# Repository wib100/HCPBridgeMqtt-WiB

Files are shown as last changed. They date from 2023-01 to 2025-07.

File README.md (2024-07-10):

# Hörmann HCPBridge with MQTT and HomeAssistant Support


Emulates Hörmann UAP1-HCP board (HCP2= Hörmann communication protocol 2) using an ESP32 and a RS485 converter, and exposes garage door controls over web page and MQTT.

**Compatible with the following motors (UAP1-HCP / HCP2-Bus / Modbus):**

* SupraMatic E/P **Serie 4**
* ProMatic **Serie 4**
* [Rollmatic v2](docs/rollmatic_v2.md)

It is **not** compatible with E**3** series motors. Previous generations have different protocol (HCP1), different pin layout, and already have another supporting project (see [hgdo](https://github.com/steff393/hgdo), [hoermann_door](https://github.com/stephan192/hoermann_door) or [hormann-hcp](https://github.com/raintonr/hormann-hcp)).

## Functions

* Get current status (door open/close/position, light on/off)
* Support for ESP32-S1/S2/S3
* Support multiple HCP Bridges for multiple garage doors
* HomeAssistant integration via MQTT-AutoDiscovery
* Trigger actions via Webinterface
  * light on/off
  * gate open, close, stop
  * gate position: half, ventilation, custom (MQTT set_position compatible)
* Configuration (Wifi, MQTT, ...) via Web Interface
* Web Service [API](#web-service)
* OTA Update (with username and password)
* First Use Hotspot for configuration
* External (optional) sensor support (threshold orientated MQTT messages):
  * DS18X20 temperature sensor
  * BME280 temperature and humidity sensor
  * DHT22 temperature and humidity sensor
  * HC-SR04 proximity sensor (car (below) detection)
  * HC-SR501 PIR motion sensor
* Efficient MQTT traffic (send only MQTT Message if states changed)

## Web Interface

***http://[deviceip]***

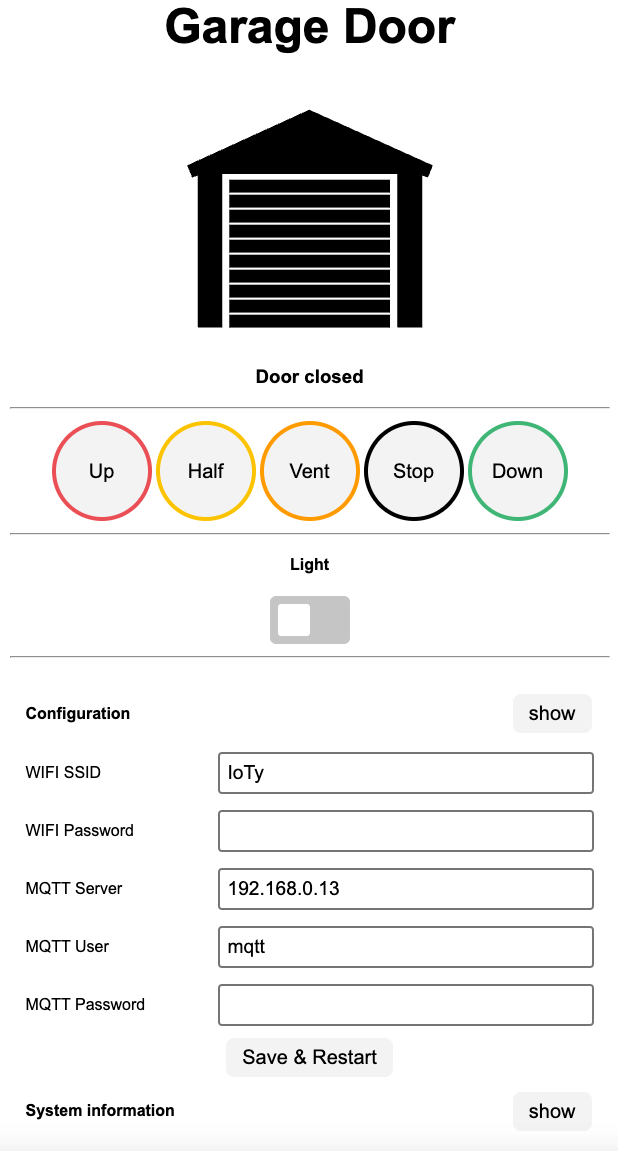
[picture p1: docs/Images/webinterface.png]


# Buy a ready to use kit [here](https://github.com/Gifford47/HCPBridgeMqtt/discussions/83) :rocket:

## ... or ...

# Build it yourself! 🔨

<details>
 <summary>Step 1: Wiring</summary>

  ## Wiring
 
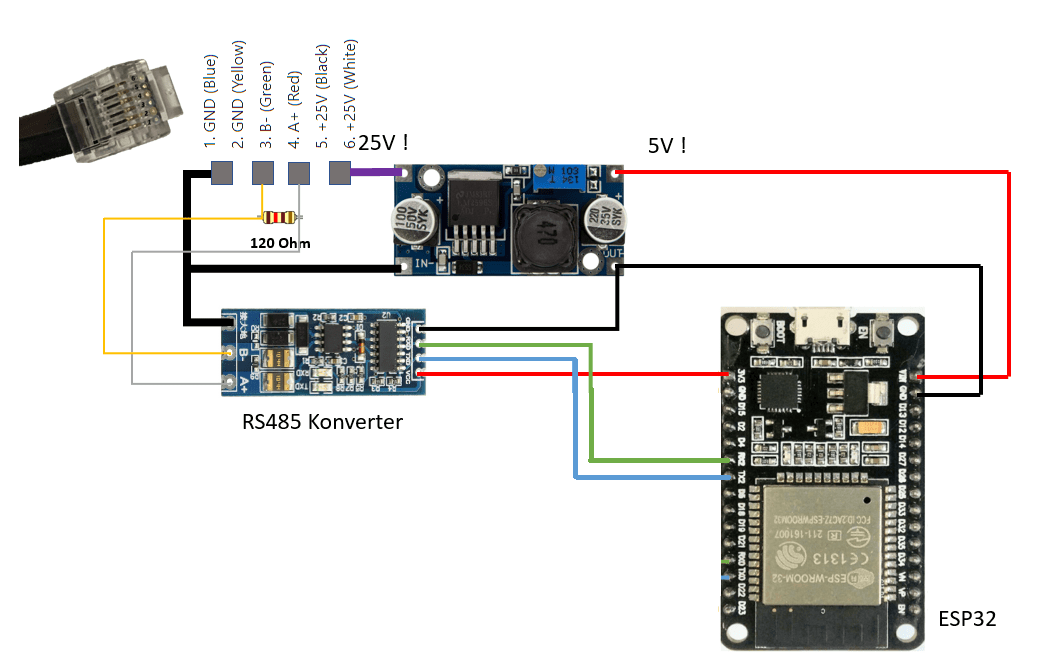
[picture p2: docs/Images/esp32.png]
min wiring
 
 
 ESP32 powering requires a Step Down Module such as LM2596S DC-DC, but any 24VDC ==> 5VDC will do, even the tiny ones with 3 pin.
 Please note that the suggested serial pins for serial interfacing, on ESP32, are 16 RXD and 17 TXD.

 <details>
 <summary>It is possible to implement it with protoboard and underside soldering:</summary>
 
 <br>
 
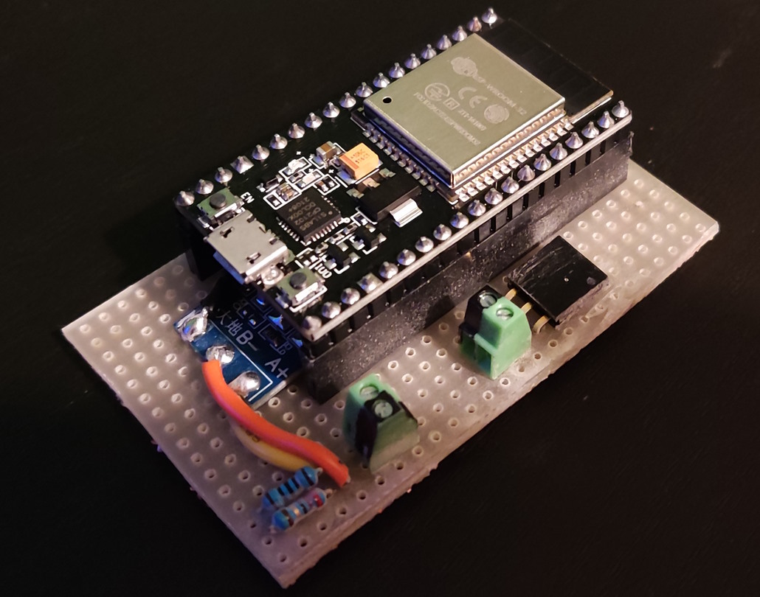
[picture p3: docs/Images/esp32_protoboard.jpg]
 
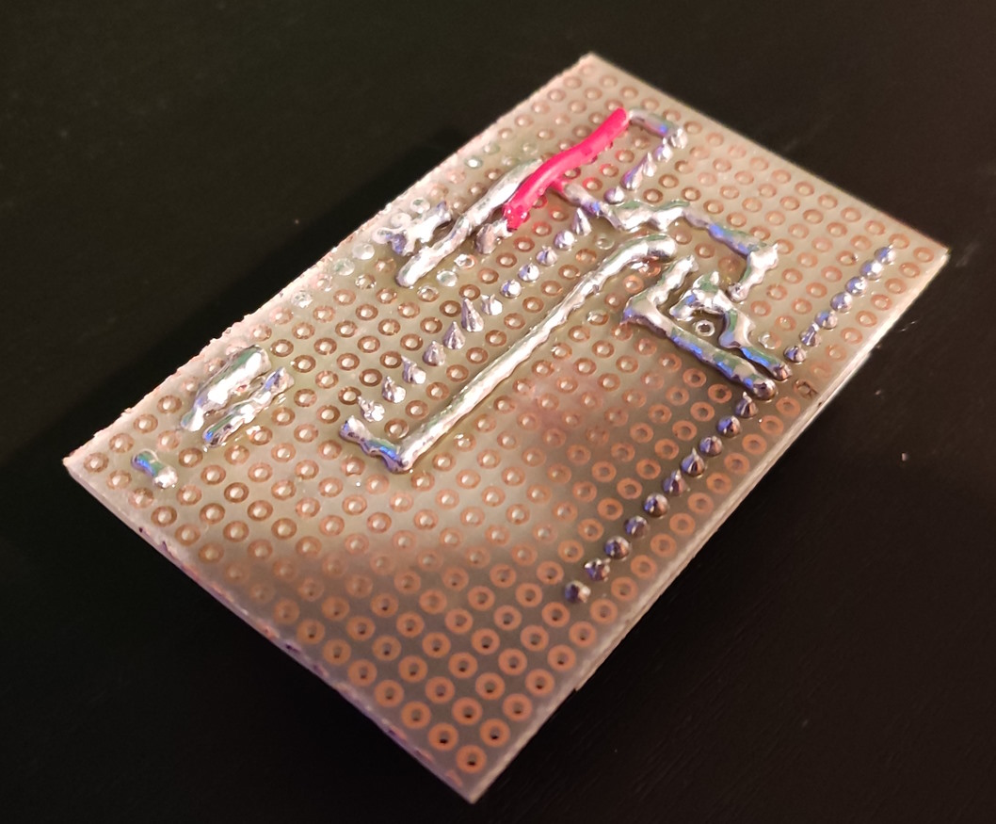
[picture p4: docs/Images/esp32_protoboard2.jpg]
 
 </details>
 
 <details>
 <summary>Details specific to Az-delivery ESP32 (ESP32-WROOM-32)</summary>
 Note the pinout on this cheap but widespread ESP32 module is a bit different. The GND on the bottom left must not be used (it is actually wrongly labeled, it should be CMD). Use the top right instead. Moreover use the pin 16 as RXD and pin 17 as TXD to match the code on this repository (using UART2, not UART0).
  
 
 
 </details>
 
 ## RS485
 
 <details open>
 <summary>Pinout RS485 Plug</summary>
 <br>
 
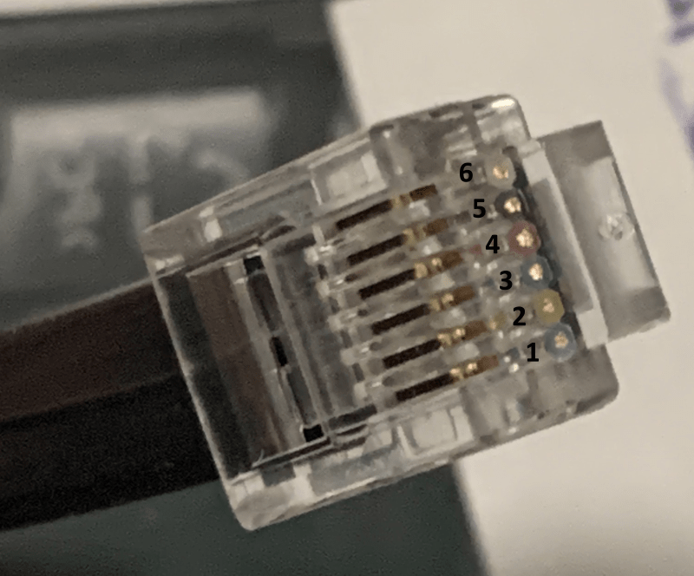
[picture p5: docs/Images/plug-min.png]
 
 
 > 📌 **Pinout**
 > 1. GND (Blue)<br>
 > 2. GND (Yellow)<br>
 > 3. B- (Green)<br>
 > 4. A+ (Red)<br>
 > 5. \+24V (Black)<br>
 > 6. \+24V (White)<br>
 
 </details>
 
 ### RS485 Adapter
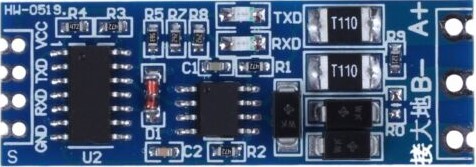
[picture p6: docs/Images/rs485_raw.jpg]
 
 > [!NOTE]<br>
 > Pins A+ (Red) and B- (Green) need a 120 Ohm resistor between them for BUS termination. Some RS485 adapters provide termination pad to be soldered.

</details><br>

<details>
 <summary>Step 2: Firmware upload</summary>
 
 ## Upload the firmware
 To use the board without any additional sensors (f.e. as showed in section [wiring](#wiring)) you only need to upload the standard firmware binary.
 ### Sensors
 
 To use additional sensors, you have also to build and upload the according firmware for the sensor. See [flash instructions](docs/flashing_instructions.md) for further info.
 <details>
 <summary>DS18X20 Temperature Sensor</summary>
 
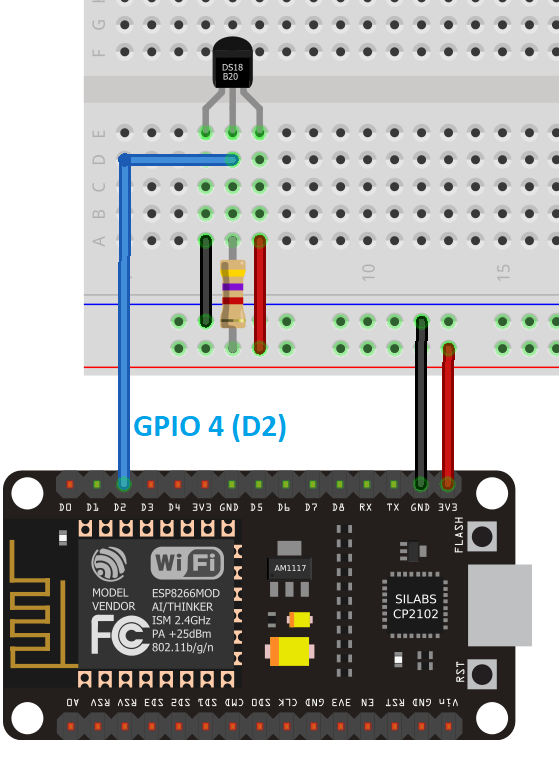
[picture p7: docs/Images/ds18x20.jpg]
  <br/>
 DS18X20 connected to GPIO4.
 <br>
 
 </details>
 
 <details>
 <summary>HC-SR501 PIR Motion sensor</summary>
 Digital out connected to GPIO23.
 <br>
 </details>
 
 <details>
 <summary>DHT22 Temperature and humudity Sensor</summary>
 Digital out connected to GPIO27.
 <br>
 </details>
 
 <details>
 <summary>BME280 Temperature and humudity Sensor</summary>
 
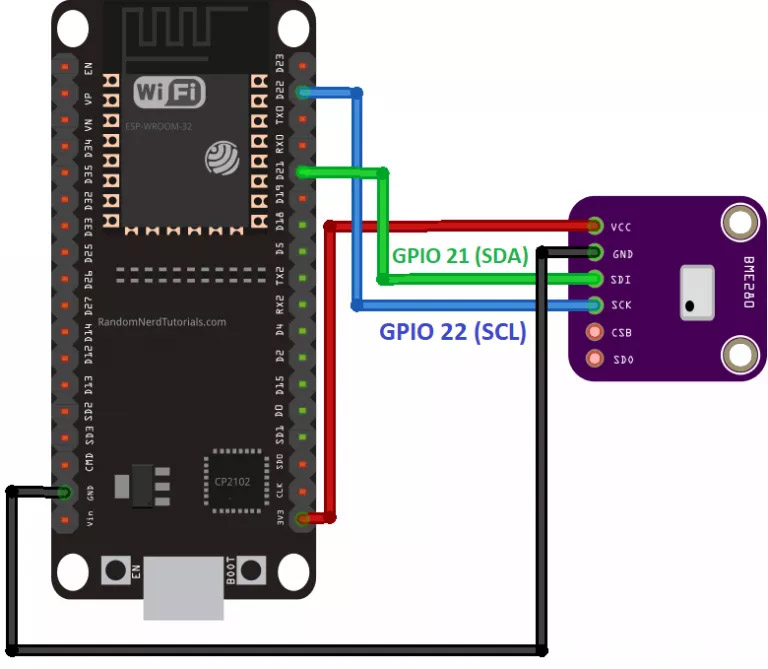
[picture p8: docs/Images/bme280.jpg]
  <br/>
 SDA connected to  GPIO21<br>
 SCL/SCK connected to GPIO22<br>
 <br>
 </details>
 
 <details>
 <summary>HC-SR04 Ultra sonic proximity sensor</summary>
 
 <br>
 Use the project task for HC-SR04.
 The wiring pins are:<br>
 SR04 Trigger pin is connected to GPIO5<br>
 SR04 ECHO pin is connected to GPIO18<br><br>
 
 It will send an mqtt discovery for two sensor one for the distance in cm available below the sensor and the other informing if the car park is available. It compare if the distance below is less than the maximal measured distance then car park is not available. The hcsr04_maxdistanceCm is defined with 150cm in configuration.h. This setting might not work for everyone. Change it to your needs.
 
 </details>
</details><br>

<details>
  <summary>Step 3: Configuration</summary>

  ## Configuration
  At first boot the settings from the configuration.h file are taken over as user preferences. If you choose to make your own build you can setup your settings there.
  After first boot you can change your settings directly in the Web interface without the need to create a new build. 
  
  With the default configuration it will open a Wifi Hotspot you can connect to. When connected to it you can use the url http://192.168.4.1 in a webbrowser to access the Web Interface and configure the device.
  
  Use the Basic Configuration section to set your wifi and MQTT credentials, after hitting the Save button your device will reboot.
  The Password fields are redacted if there are set with a *. If you don't want to change it just leave the * as it will be interpretet as no change.
  
  
  
  The preferences will stay even after a OTA update.
  When the memory of your ESP get's deleted your ESP will again load the settings from the configuration.h file.
  
  You can reset all preferences by pressing the BOOT button on the ESP for longer then 5 Seconds and releasing it.
  This will reset all preferences to the default values from configuration.h in the flashed firmware build.
  
  ## Web Services
  
  <details>
  <summary>Send commands</summary>
  
  URL: **http://[deviceip]/command?action=[id]**
  <br>
  
  | id | Function | Other Parameters
  |--------|--------------|--------------|
  | 0 | Close | |
  | 1 | Open | |
  | 2 | Stop | |
  | 3 | Ventilation | |
  | 4 | Half Open | |
  | 5 | Light toggle | |
  | 6 | Restart | |
  | 7 | Set Position | position=[0-100] |
  
  </details>
  
  <details>
  <summary>Status report</summary>
  
  URL: **http://[deviceip]/status**
  <br>
  
  Response:
  ```
  {
  "valid": true,
  "doorstate": 64,
  "doorposition": 0,
  "doortarget": 0,
  "lamp": false,
  "temp": 19.94000053,
  "lastresponse": 0,
  "looptime": 1037,
  "lastCommandTopic": "hormann/garage_door/command/door",
  "lastCommandPayload": "close"
  }
  ```
  </details>
  
  <details>
  <summary>Wifi status</summary>
  
  URL: **http://[deviceip]/sysinfo**
  <br>
  </details>
  
  <details>
  <summary>OTA Firmware update</summary>
  
  URL: **http://[deviceip]/update**
  <br>
  
  
  
  </details><br>
  
  </details><br>

<details>
  <summary>Step 4: Installation and Bus Scan</summary>
 
  ## Installation
  
  * Connect the board to the BUS
  * Run a BUS scan (differs on the following hardware version): 
  
  ### Old Hardware version
  
  BUS scan is started through flipping (ON - OFF) last dip switch. Note that BUS power  (+24v) is removed when no devices are detected. In case of issues, you may find useful to "jump start" the device using the +24V provision of other connectors of the motor control board.
    
  ### New Hardware version 
  With newer HW versions, the bus scan is carried out using the LC display in menu 37. For more see: [Supramatic 4 Busscan](https://www.tor7.de/news/bus-scan-beim-supramatic-serie-4-fehlercode-04-vermeiden)
  
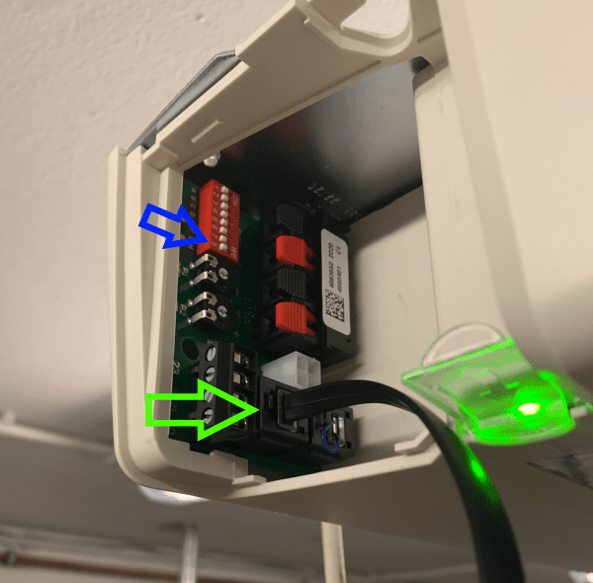
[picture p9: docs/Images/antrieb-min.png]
  
</details><br>

## Set the ventilation position 

This is just a quick and dirty implementation and needs refactoring, but it is working.
Using the Shutter Custom Card (from HACS) it is also possible to get a representation of the current position of the door, and slide it to custom position (through set_position MQTT command).

The switch for the venting position works with a small hack. Based on the analyses of dupas.me the motor should gave a status 0x0A in venting position. As this was not the case the variable VENT_POS in hciemulator.h was default with value '0x08' which correspond to the position when the garage door is in venting position (position available under ***http://[deviceip]/status***). When the door is stopped in this position the doorstate is set as venting.

<details>
<summary>HomeAssistant shutter cards</summary>

<br>

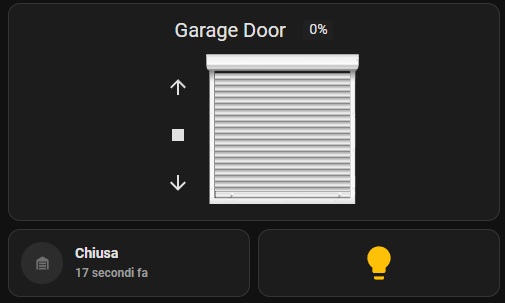
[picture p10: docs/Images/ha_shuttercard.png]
Homeassistant card1

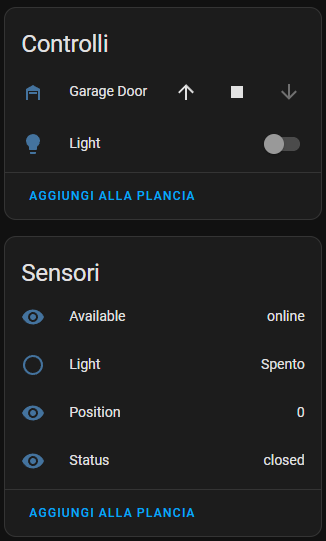
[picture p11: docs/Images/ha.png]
Homeassistant card2

</details>

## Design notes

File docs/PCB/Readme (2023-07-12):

Many thanks @vladimirzrnic for sharing his PCB design.

In the archive folder you will find a working design but to big to fit in the enclosure.

Please always check your wiring as depending on the cable or on the connector on the board the wires could be inverted. More detailed howto will follow

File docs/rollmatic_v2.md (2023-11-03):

# Rollmativ V2

## Hardware part:

* Remove power cord
* Plug in RJ-11 connector
* Plug-in power cord
* Drive the garage door completely up or down once

## Programming:

* Hold "PGR" button until 10 is shown
* Press "Down" button until "37" is shown
* Press "PRG" button once -> Display shows "00" (meaning "no external modules configured")
* Press "Up" button once until 01 is shown (meaning "configure external module")
* Hold "PGR" button until "B.S." is shown
* When "B.S." starts blinking, bus scan is running (RX and TX on RS485 board active)
* If external module was recognized on the bus, the display shows "1" for a couple of seconds
* If external module was not recognized on the bus, the display shows "01" or "00" for a couple of seconds
* Menu goes back to "10"

## Troubleshooting Error "04"
Hörmann Rollmatic v2 uses HCP2-Bus which requires external modules to be registered and unregistered via bus scan. Error "04" shows up when you want to drive the door, but the registered external module was removed without performing a bus scan afterwards. The door will not drive until the issue is solved.

This can be archieved by Powering off the door, re-attach the external module and power on again.
Or by performing a complete factory reset of the Rollmatic v2.

Unfortunately a simple un-registration of a registered (but non working or non-attached module) seems not possible since in my case, Error "04" prevents access to the programming menu after powering on.

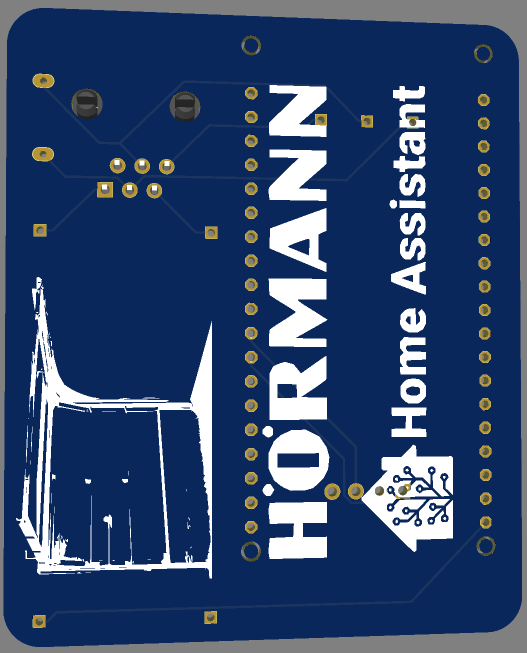
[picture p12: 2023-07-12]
docs/PCB/vladimirzrnic/back.png

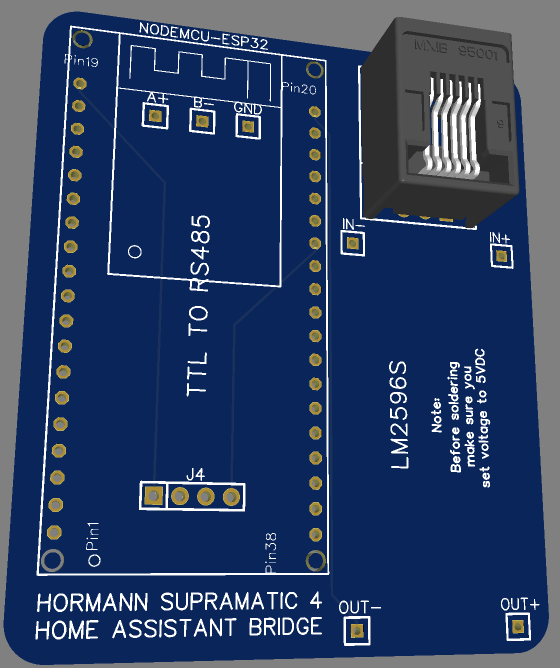
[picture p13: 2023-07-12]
docs/PCB/vladimirzrnic/top.png

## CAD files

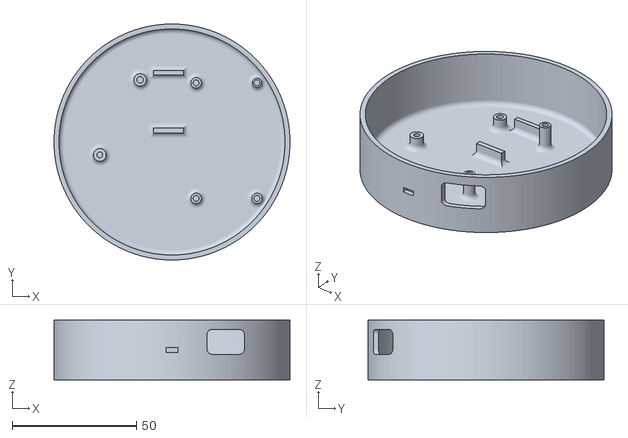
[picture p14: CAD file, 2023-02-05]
docs/3d/body.STL
95.0 x 95.0 x 24.0

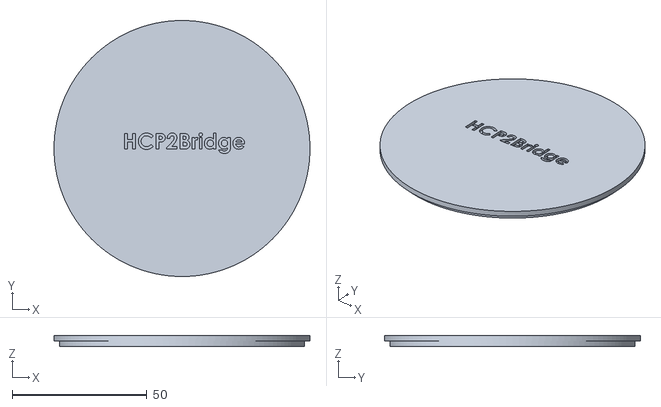
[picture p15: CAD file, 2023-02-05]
docs/3d/lid.STL
95.0 x 95.0 x 4.00

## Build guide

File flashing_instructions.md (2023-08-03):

# How to Flash the Firmware

## Setup Software

Download and install VS Code from Microsoft to your Computer: https://code.visualstudio.com/download

After that open VS Code and go to extensions, search for Platform IO and install it, follow any instructions if a restart or something is needed

## Get Firmware

On the Main Repo click the green Get Code Button and download the firmware as a zip.
Extract the Zip File and remember where you put it on your Computer.
Go to VSCode, click the PlatformIO Symbol at the bottom to switch to the Plugin UI.
Click the Open Folder button and select the HCPBridgeESp32 Folder inside the extracted Firmware.

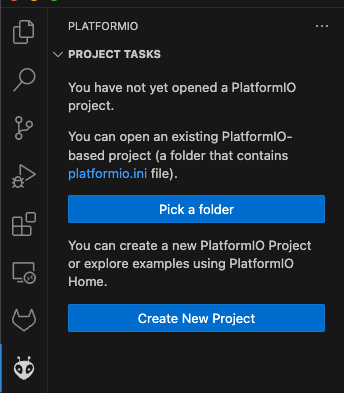
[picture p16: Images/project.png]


## Configuration

Use the left Sidebar again and click on the Folder Symbol to switch to the File List.
Before you can flash the Firmware you will need to change the Configuration in the configuration.h File located in the src Folder.

You need to set your WIFi Name/SSID and Password as well as the Connection Details to your MQTT Server if you want to use that Feature.

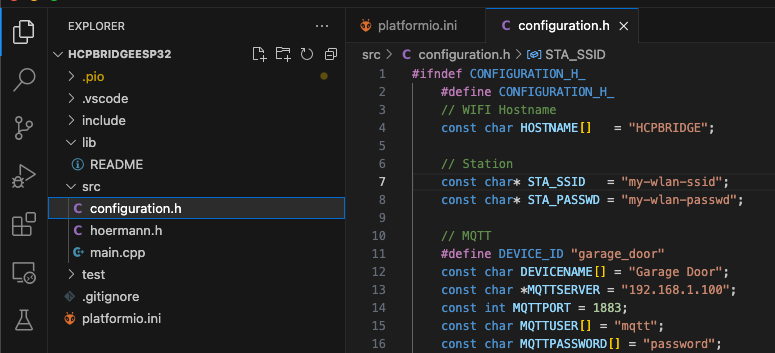
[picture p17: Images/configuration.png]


## Build and Flash

Go back to the Platform IO UI and click on the ESP Model you got under "Project Tasks".
ESP32 for older Boards and ESP32S3 for newer Boards (for example all PCBs with a Tynet logo)
Open the General Tasks of the Board you got and click Build.

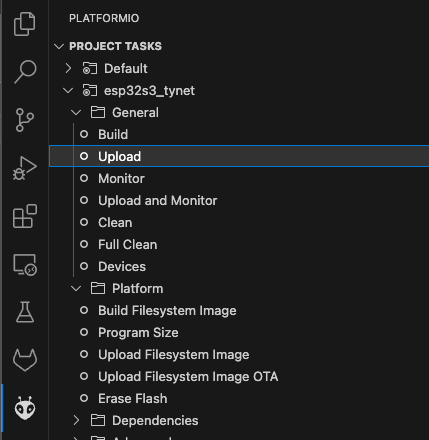
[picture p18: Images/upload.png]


This should prepare the Firmware for your Board including your Configuration, if all goes well the Terminal will show a green success message.

If this works you can connect your Device and click the Upload Task to flash it, this should also result in a Success info in green text inside the Terminal.

After this you can replug your device from USB to restart it and it should connect to your WIFI Router and MQTT Server.

Now you can connect it via the RJ12 cable to your garage door and start the BUS Scan, if all works the two communication leds should blink fast.
With this the MQTT as well as web controls on the devices IP should also work and you are Done :)

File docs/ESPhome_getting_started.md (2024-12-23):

# Getting started with the ESPHome version

Our boards from tynet.eu ship with the normal Arduino based Firmware that is simple to use out of the box.
Sadly this software that was developed over the past years got some minor inconveniences that are not simple to fix.
If you are one of the few people that have an issue with th software or just wan't to use ESPHome instead you can follow this guide

ESPHome uses a native Home Assistant API instead of MQTT and is simple to setup, we also porivde configuration files as well as ready to flash bin files for our boards.

## Setup ESPHome in Home Assistant

You can follow the [official guide](https://esphome.io/guides/getting_started_hassio) to install the ESPHome Add-on for Home Assistant.

The main steps are:

1. Open your Home Assitant UI
2. Go to Settings->Add-Ons->Add-on Store and search for ESPHome
3. Install and activate the ESPHome addon

## Upgrade from non ESPHome firmware

Our boards all ship with a non ESPHome based firmware, it can be upgraded really simple.

1. Ensure your board is powered over USB-C 
2. Download ESPHome based firmware file: [hcpbridge.ota.bin](https://github.com/Tysonpower/HCPBridgeMqtt_tynet/raw/refs/heads/main/hcpbridge.ota.bin)
3. Connect to your board and open the OTA webui: [http://192.168.4.1/update](http://192.168.4.1/update)
4. If asked use the following credentials to login: `user: admin pass: admin`
5. Click "Select File", navigate to the downloaded ota file from step 1, 

## Board Setup

### Using USB (recommended)

1. Ensure your board is connected to your PC over USB-C
2. Open [web.ESPHome.io](https://web.esphome.io), click connect, select the ESP32-S3 device from the list
3. Click the 3 point menu and select Configure Wifi, select or anter your wifi name and password


4. After entering your wifi credentials click connect


### Using WiFi

1. Ensure your board is powered over USB-C
2. Search and connect to the wifi called `hcpbridge`
3. Open http://192.168.4.1 when connected, login is `user: admin pass: tynet.eu`
4. Connect to your wifi network over the UI
____

Now your board should be connected to your home network over wifi.

Open home Assistant, go to Devices, here the garage door should be visible under discovered devices, just click "Add".



## Change preflashed config (Optional)

1. open home assistant and go to the ESPHome UI under Add-Ons
2. You should see the dicovered device, press take control. if you like, change the name


4. it will ask to update the device with encryption, click install, it will take a wile to build the new firmware


5. When it finished uploading you will see the following log output, if this is the case you can press close and you are done


In some cases you need to set your wifi credentials again afterwards like before

## Setup ESPHome in Home Assistant from scratch

1. Open ESPHome in Home Assistant
2. Connect your board only via usb to your PC
3. Click "New Device" and enter a name


4. Click ESP32-S3


5. Copy and save the displayed encryption key and click skip


6. Click on the secrets button on the top right, create the following keys and enter your wifi credentials as well as the secret api key you just copied, hit save

```
wifi_ssid: "myWifi"
wifi_password: "myWifiPassword"
api_key: "myApiSecretWeCopiedAfewMinutesAgo"
web_username: "admin"
web_password: "tynet.eu"
hcp_wifi_ap_password: "tynet.eu"
```

7. Click Edit on the device card


8. Copy paste the content of the ESPHome.yaml file from this repo into the editor, click save


9. Click install, then select Manual download, wait for the firmware to be build, select factory format to get the.bin file




10. Then go to [web.ESPHome.io](https://web.esphome.io/), click connect and select your ESP from the device list, click INSTALL, select the .bin file you just downloaded and click Install.
If it doesen't work, try it multiple times


11. go back to home assistant, open settings->devices->ESPHome, here you should be able to add the device, if not try to powercycle the board


Click done and you can now use the Device


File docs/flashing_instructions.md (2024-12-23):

# How to Flash the Firmware

## Setup Software

Download and install VS Code from Microsoft to your Computer: https://code.visualstudio.com/download

After that open VS Code and go to extensions, search for Platform IO and install it, follow any instructions if a restart or something is needed

## Get Firmware

On the Main Repo click the green Get Code Button and download the firmware as a zip.
Extract the Zip File and remember where you put it on your Computer.
Go to VSCode, click the PlatformIO Symbol at the bottom to switch to the Plugin UI.
Click the Open Folder button and select the HCPBridgeESp32 Folder inside the extracted Firmware.



## Configuration

In this step you can preset the preferences. On first boot they will be stored on the Memory of the ESP. 
After you have to change it from the WEB ui or Reset the ESP memory to load again the data from the configuration file.
Use the left Sidebar again and click on the Folder Symbol to switch to the File List.
Before you can flash the Firmware you will need to change the Configuration in the configuration.h File located in the src Folder.

You need to set your WIFi Name/SSID and Password as well as the Connection Details to your MQTT Server if you want to use that Feature.



## Build and Flash

Go back to the Platform IO UI and click on the ESP Model you got under "Project Tasks".
ESP32 for older Boards and ESP32S3 for newer Boards (for example all PCBs with a Tynet logo)
Open the General Tasks of the Board you got and click Build.



This should prepare the Firmware for your Board including your Configuration, if all goes well the Terminal will show a green success message.

If this works you can connect your Device and click the Upload Task to flash it, this should also result in a Success info in green text inside the Terminal.

After this you can replug your device from USB to restart it and it should connect to your WIFI Router and MQTT Server.

Now you can connect it via the RJ12 cable to your garage door and start the BUS Scan, if all works the two communication leds should blink fast.
With this the MQTT as well as web controls on the devices IP should also work and you are Done :)

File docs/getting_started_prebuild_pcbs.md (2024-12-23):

# Getting started with prebuild PCBs

If you bought a prebuild PCB from either Tynet.eu or someone else you can follow this setp by step guide to setup your HCP-Bridge with your Hörmann Garage Door.
These instructions focus on the tynet.eu PCB version, but it will be really similar with all PCBs.

You want to connect temperature sensors or something else? See our guide: [Connecting sensors on tynet boards](connecting_sensors_prebuild_pcbs.md)

## What you need

* Prebuild PCB with HCPBridge Firmware installed (installed out of the box on tynet.eu PCBs)
* USB-C power supply

## Initial configuration

### 1. Connect the PCB to power via the USB-C connector and wait a few seconds. the 3V3 LED will be lit.
### 2. Search and connect to the WIFI Network called "HCPBRIDGE" the PCB creates with a phone or pc.
### 3. When connected, open a webbrowser and go to the WEBUI under the following url : http://192.168.4.1

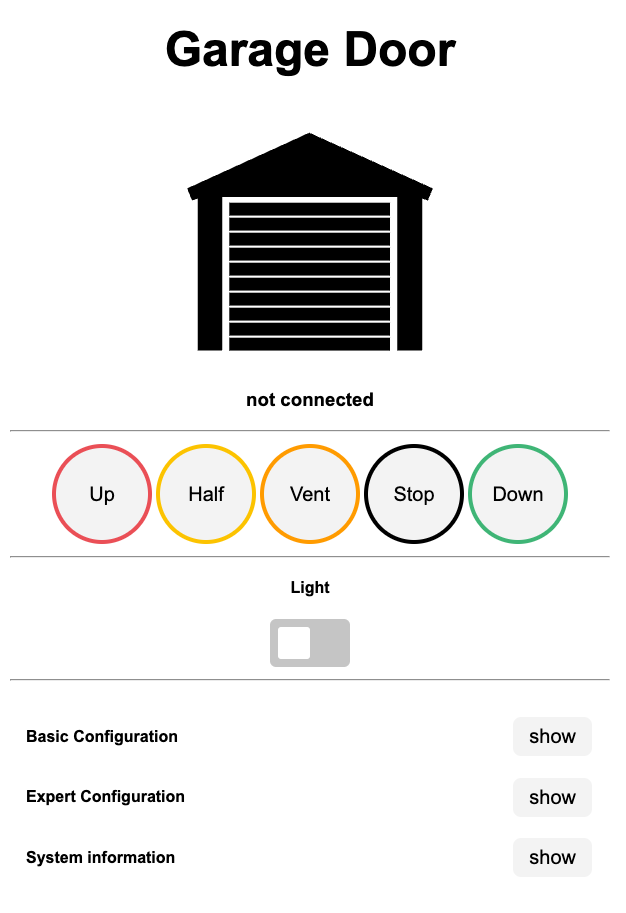
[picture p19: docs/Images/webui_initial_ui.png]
Initial WebUI


### 4. Open the "Basic Configuration" tab and enter your WIFI and MQTT credentials, then click save.

> Note: The wifi password has to be ASCII chars between ASCII 32-126.

> Tip: To disable the wifi AP just uncheck the "Enable wifi AP" checkbox and save

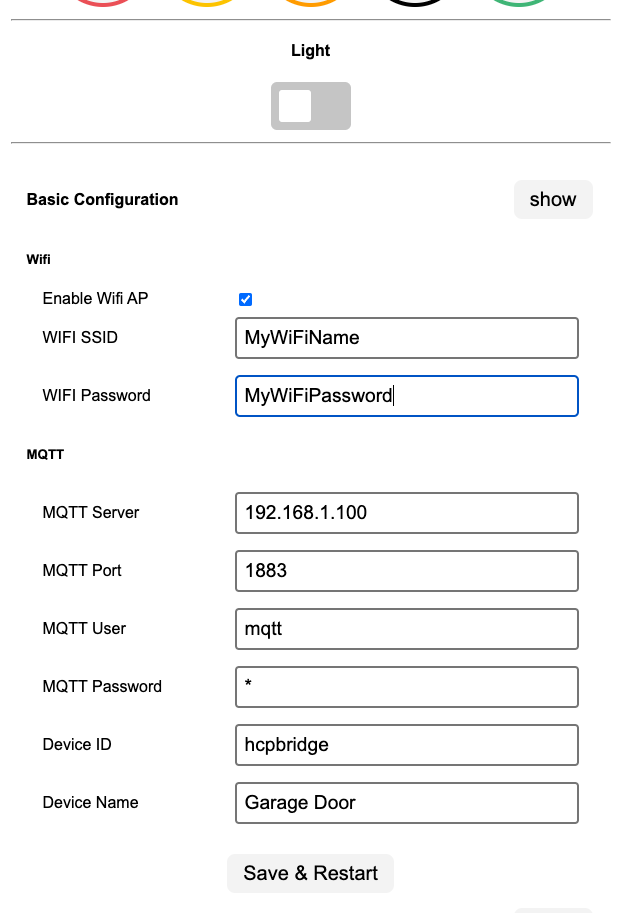
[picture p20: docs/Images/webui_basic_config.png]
basic config


### 5. The PCB should now be connected to your wifi. You can now check if it is reachable from your home network and if it connected to your MQTT Server.

## Installation

### 1. connect the PCB with a RJ12 cable to the BUS port on your Hörmann garage door motor (image below, see green arrow).

Garage Motor
   
### 2. Figure out how to execute a bus scan on your model, see info below or have a look in your motors ueer manual.

**ProMatic Serie 4**

Use the bottom dip switch (see image above, blue arrow) and toggle it, this will start the buss can.

**SupraMatic E/P Serie 4**

Use the Buttons to navigate to the menu 37 and excecute the Bus Scan, see here: [Tor7.de - Supramatic Bus Scan](https://www.tor7.de/news/bus-scan-beim-supramatic-serie-4-fehlercode-04-vermeiden)
  
### 3. execute a bus scan on your garage door motor, this should make the PCB light up (3V3) and blink rapidly (RS485 module)
### 4. if the bus scan was succesfully you can connect to the WEBUI and control your garage door motor, it should look like in the image below.

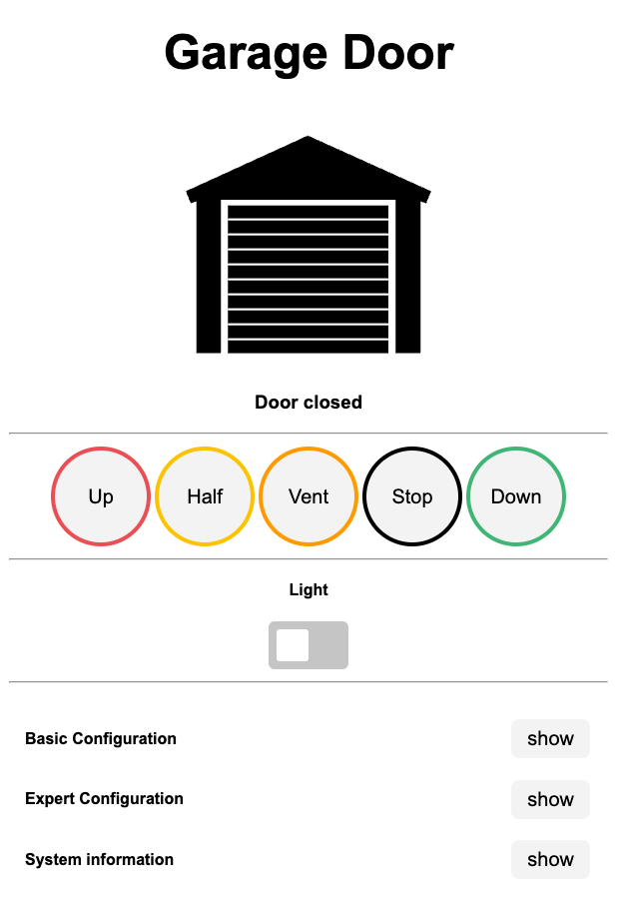
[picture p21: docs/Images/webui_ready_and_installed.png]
Installation done


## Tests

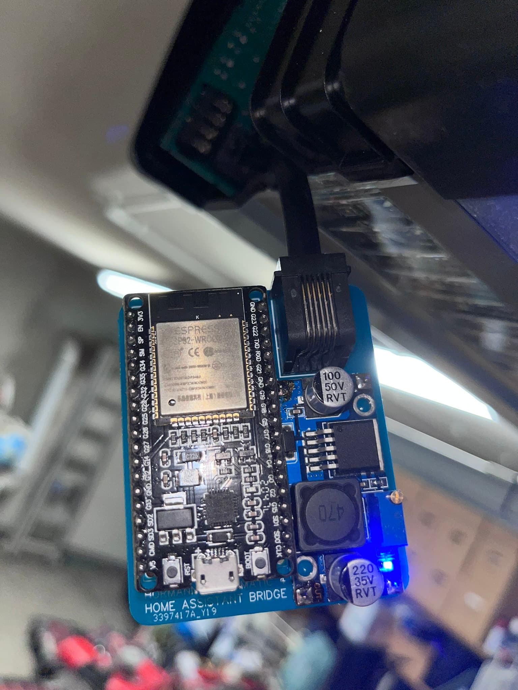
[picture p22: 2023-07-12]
docs/PCB/vladimirzrnic/result.JPEG

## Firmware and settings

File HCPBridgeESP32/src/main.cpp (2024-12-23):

#include <Arduino.h>
#include <Esp.h>
#include <ElegantOTA.h>
#include <ESPAsyncWebServer.h>
#include "AsyncJson.h"
#include <AsyncMqttClient.h>
extern "C" {
	#include "freertos/FreeRTOS.h"
	#include "freertos/timers.h"
}
#include "ArduinoJson.h"

#include "hoermann.h"
#include "preferencesKeys.h"
#include "../WebUI/index_html.h"

#ifdef USE_DS18X20
  #include <OneWire.h>
  #include <DallasTemperature.h>
#endif

#ifdef USE_BME
  #include <Wire.h>
  #include <Adafruit_Sensor.h>
  #include <Adafruit_BME280.h>
#endif

#ifdef USE_DHT22
  #include <Adafruit_Sensor.h>
  #include <DHT.h>
#endif

// webserver on port 80
AsyncWebServer server(80);

#ifdef SENSORS
  int     sensor_prox_tresh   = 0;
  float  sensor_temp_thresh  = 0;
  int     sensor_hum_thresh   = 0;
  int     sensor_pres_thresh  = 0;
  int     sensor_last_update  = 0;
  int     sensor_force_update_intervall = 7200000;    // force sending sensor updates after amount of time since last update
#endif


#ifdef USE_DS18X20
  // Setup a oneWire instance to communicate with any OneWire devices
  DallasTemperature *ds18x20 = nullptr;
  float ds18x20_temp = -99.99;
  float ds18x20_last_temp = -99.99;
  int ds18x20_pin = 0;
#endif
#ifdef USE_BME
  TwoWire I2CBME = TwoWire(0);
  Adafruit_BME280 bme;
  unsigned bme_status;
  float bme_temp = -99.99;
  float bme_last_temp = -99.99;
  float bme_hum = -99.99;
  float bme_last_hum = -99.99;
  float bme_pres = -99.99;
  float bme_last_pres = -99.99;
  int i2c_sdapin = 0;
  int i2c_sclpin = 0;
#endif

#ifdef USE_HCSR04
  long hcsr04_duration = -99.99;
  int hcsr04_distanceCm = 0;
  int hcsr04_lastdistanceCm = 0;
  int hcsr04_maxdistanceCm = 150;
  bool hcsr04_park_available = false;
  bool hcsr04_lastpark_available = false;
  int hcsr04_tgpin = 0;
  int hscr04_ecpin = 0;
#endif

#ifdef USE_DHT22
  DHT *dht = nullptr;
  float dht22_temp = -99.99;
  float dht22_last_temp = -99.99;
  float dht22_hum = -99.99;
  float dht22_last_hum = -99.99;
  int dht_data_pin = 0;
#endif

#ifdef USE_HCSR501
  int hcsr501stat = 0;
  bool hcsr501_laststat = false;
#endif

// sensors
bool new_sensor_data = false;

// mqtt
volatile bool mqttConnected;
AsyncMqttClient mqttClient;
TimerHandle_t mqttReconnectTimer;
TimerHandle_t wifiReconnectTimer;

char lastCommandTopic[64];
char lastCommandPayload[64];

PreferenceHandler prefHandler;
Preferences *localPrefs = nullptr;

class MqttStrings {    
  public:         
    char availability_topic [64];
    char state_topic [64];
    char cmd_topic [64];
    char pos_topic [64];
    char setpos_topic [64];
    char lamp_topic [64];
    char door_topic [64];
    char vent_topic [64];
    char sensor_topic [64];
    char debug_topic [64];
    String st_availability_topic;
    String st_state_topic;
    String st_cmd_topic;
    String st_cmd_topic_var;
    String st_cmd_topic_subs;
    String st_pos_topic;
    String st_setpos_topic;
    String st_lamp_topic;
    String st_door_topic;
    String st_vent_topic;
    String st_sensor_topic;
    String st_debug_topic;   
};
MqttStrings mqttStrings;

unsigned long resetButtonTimePressed = 0l;
TimerHandle_t resetTimer;

#ifdef DEBUG
  bool boot_Flag = true;
#endif

const char *ToHA(bool value)
{
  if (value == true)
  {
    return HA_ON;
  }
  if (value == false)
  {
    return HA_OFF;
  }
  return "UNKNOWN";
}

void setuptMqttStrings(){
  String ftopic = "hormann/" + localPrefs->getString(preference_gd_id);
  mqttStrings.st_availability_topic = ftopic + "/availability";
  mqttStrings.st_state_topic = ftopic + "/state";
  mqttStrings.st_cmd_topic = ftopic + "/command";
  mqttStrings.st_cmd_topic_var = mqttStrings.st_cmd_topic + "/%s";
  mqttStrings.st_cmd_topic_subs = mqttStrings.st_cmd_topic + "/#";
  mqttStrings.st_pos_topic = ftopic + "/position";
  mqttStrings.st_setpos_topic = mqttStrings.st_cmd_topic  + "/set_position";
  mqttStrings.st_lamp_topic = mqttStrings.st_cmd_topic  + "/lamp";
  mqttStrings.st_door_topic = mqttStrings.st_cmd_topic  + "/door";
  mqttStrings.st_vent_topic = mqttStrings.st_cmd_topic  + "/vent";
  mqttStrings.st_sensor_topic = ftopic + "/sensor";
  mqttStrings.st_debug_topic = ftopic + "/debug";

  strcpy(mqttStrings.availability_topic, mqttStrings.st_availability_topic.c_str());
  strcpy(mqttStrings.state_topic, mqttStrings.st_state_topic.c_str());
  strcpy(mqttStrings.cmd_topic, mqttStrings.st_cmd_topic.c_str());
  strcpy(mqttStrings.pos_topic, mqttStrings.st_pos_topic.c_str()); 
  strcpy(mqttStrings.setpos_topic, mqttStrings.st_setpos_topic.c_str());
  strcpy(mqttStrings.lamp_topic, mqttStrings.st_lamp_topic.c_str());
  strcpy(mqttStrings.door_topic, mqttStrings.st_door_topic.c_str());
  strcpy(mqttStrings.vent_topic, mqttStrings.st_vent_topic.c_str());
  strcpy(mqttStrings.sensor_topic, mqttStrings.st_sensor_topic.c_str());
  strcpy(mqttStrings.debug_topic, mqttStrings.st_debug_topic.c_str());
}

void IRAM_ATTR reset_button_change(){
  if (digitalRead(0) == 0)
  {
    // Pressed
    resetButtonTimePressed = millis();
  } else {
    // unpressed
    unsigned long timeNow = millis();
    int timeInSecs = (timeNow - resetButtonTimePressed) / 1000;
    if (timeInSecs > 5)
    {
      xTimerStart(resetTimer, 0);
    }
    resetButtonTimePressed = 0;
  }
}

void resetPreferences()
{
  xTimerStop(resetTimer, 0);
  Serial.println("Resetting config...");
  //prefHandler.resetPreferences();
}

void switchLamp(bool on){
  hoermannEngine->turnLight(on);
}

void connectToWifi() {
  /*if (localPrefs->getBool(preference_wifi_ap_mode))
  {
    Serial.println("WIFI AP mode enabled, set Hostname");
    WiFi.softAP(prefHandler.getPreferencesCache()->hostname);
    return;
  }*/
  if (localPrefs->getString(preference_wifi_ssid) != "")
  {
    Serial.println("Connecting to Wi-Fi...");
    WiFi.begin(localPrefs->getString(preference_wifi_ssid).c_str(), localPrefs->getString(preference_wifi_password).c_str());
  } else
  {
    Serial.println("No WiFi Client enabled");
  }

  //Serial.println("Connecting to Wi-Fi...");
  //this disocnnect should not be necessary as we restart the esp after changing form AP mode to Station mode.
  //WiFi.softAPdisconnect(true);  //stop AP, we now work as a wifi client

}
void connectToMqtt()
{
  Serial.println("Connecting to MQTT...");
  mqttClient.connect();
}

void onMqttDisconnect(AsyncMqttClientDisconnectReason reason)
{
  mqttConnected = false;
  #ifdef DEBUG
  switch (reason) {
    case AsyncMqttClientDisconnectReason::TCP_DISCONNECTED: 
      Serial.println("Disconnected from MQTT. reason : TCP_DISCONNECTED");
      break;
    case AsyncMqttClientDisconnectReason::MQTT_UNACCEPTABLE_PROTOCOL_VERSION: 
      Serial.println("Disconnected from MQTT. reason : MQTT_UNACCEPTABLE_PROTOCOL_VERSION");
      break;
    case AsyncMqttClientDisconnectReason::MQTT_IDENTIFIER_REJECTED: 
      Serial.println("Disconnected from MQTT. reason : MQTT_IDENTIFIER_REJECTED");
      break;
    case AsyncMqttClientDisconnectReason::MQTT_SERVER_UNAVAILABLE: 
      Serial.println("Disconnected from MQTT. reason : MQTT_SERVER_UNAVAILABLE");
      break;
    case AsyncMqttClientDisconnectReason::ESP8266_NOT_ENOUGH_SPACE: 
      Serial.println("Disconnected from MQTT. reason : ESP8266_NOT_ENOUGH_SPACE");
      break;
    case AsyncMqttClientDisconnectReason::MQTT_MALFORMED_CREDENTIALS: 
      Serial.println("Disconnected from MQTT. reason : MQTT_MALFORMED_CREDENTIALS");
      break;
    case AsyncMqttClientDisconnectReason::MQTT_NOT_AUTHORIZED: 
      Serial.println("Disconnected from MQTT. reason : MQTT_NOT_AUTHORIZED");
      break;
    case AsyncMqttClientDisconnectReason::TLS_BAD_FINGERPRINT: 
      Serial.println("Disconnected from MQTT. reason :TLS_BAD_FINGERPRINT");
      break;
    default: break;
  } 
  #endif


  if (WiFi.isConnected()) {
    xTimerStart(mqttReconnectTimer, 0);
  }
}

void onMqttPublish(uint16_t packetId){
}

void updateDoorStatus(bool forceUpate = false)
{
  // onyl send updates when state changed
  if (hoermannEngine->state->changed || forceUpate){
    hoermannEngine->state->clearChanged();
    JsonDocument doc;
    char payload[1024];
    const char *venting = HA_CLOSE;

    doc["valid"] = hoermannEngine->state->valid;
    doc["doorposition"] = (int)(hoermannEngine->state->currentPosition * 100);
    doc["lamp"] = ToHA(hoermannEngine->state->lightOn);
    doc["doorstate"] = hoermannEngine->state->coverState;
    doc["detailedState"] = hoermannEngine->state->translatedState;
    if (hoermannEngine->state->translatedState == HA_VENT){
      venting = HA_VENT;
    }
    doc["vent"] = venting;

    serializeJson(doc, payload);
    mqttClient.publish(mqttStrings.state_topic, 1, true, payload);

    sprintf(payload, "%d", (int)(hoermannEngine->state->currentPosition * 100));
    mqttClient.publish(mqttStrings.pos_topic, 1, true, payload);
  }
}

void updateSensors(bool forceUpate = false){
  #ifdef SENSORS
    if (millis()-sensor_last_update >= sensor_force_update_intervall) {
      forceUpate = true;
    }
    
    if (new_sensor_data || forceUpate) {
      new_sensor_data = false;
      JsonDocument doc;    //2048 needed because of BME280 float values!
      char payload[1024];
      char buf[20];
      #ifdef USE_DS18X20
        dtostrf(ds18x20_temp,2,1,buf);    // convert to string
        //Serial.println("Temp: "+ (String)buf);
        doc["temp"] = buf;
      #endif
      #ifdef USE_BME
        dtostrf(bme_temp,2,1,buf);    // convert to string
        //Serial.println("Temp: "+ (String)buf);
        doc["temp"] = buf;
        dtostrf(bme_hum,2,1,buf);    // convert to string
        //Serial.println("Hum: "+ (String)buf);
        doc["hum"] = buf;
        dtostrf(bme_pres,2,1,buf);    // convert to string
        //Serial.println("Pres: "+ (String)buf);
        doc["pres"] = buf;
      #endif
      #ifdef USE_HCSR04
        sprintf(buf, "%d", hcsr04_distanceCm);
        doc["dist"] = buf;
        doc["free"] = ToHA(hcsr04_park_available);
      #endif
      #ifdef USE_DHT22
        dtostrf(dht22_temp,2,2,buf);
        doc["temp"] = buf;
        dtostrf(dht22_hum,2,2,buf);
        doc["hum"] = buf;
      #endif
      serializeJson(doc, payload);
      mqttClient.publish(mqttStrings.sensor_topic, 0, false, payload);  //uint16_t publish(const char* topic, uint8_t qos, bool retain, const char* payload = nullptr, size_t length = 0)
      sensor_last_update = millis();
    }
  #endif
}

void onMqttMessage(char *topic, char *payload, AsyncMqttClientMessageProperties properties, size_t len, size_t index, size_t total)
{
  // Note that payload is NOT a string; it contains raw data.
  // https://github.com/marvinroger/async-mqtt-client/blob/develop/docs/5.-Troubleshooting.md
  strcpy(lastCommandTopic, topic);
  strncpy(lastCommandPayload, payload, len);
  lastCommandPayload[len] = '\0';

  if (strcmp(topic, mqttStrings.lamp_topic) == 0){
    if (strncmp(payload, HA_ON, len) == 0){
      switchLamp(true);
    }
    else if (strncmp(payload, HA_OFF, len) == 0){
      switchLamp(false);
    }
    else{
      hoermannEngine->toogleLight();
    }
  }
  else if (strcmp(mqttStrings.door_topic, topic) == 0 || strcmp(mqttStrings.vent_topic, topic) == 0){
    if (strncmp(payload, HA_OPEN, len) == 0){
      hoermannEngine->openDoor();
    }
    else if (strncmp(payload, HA_CLOSE, len) == 0){
      hoermannEngine->closeDoor();
    }
    else if (strncmp(payload, HA_STOP, len) == 0){
      hoermannEngine->stopDoor();
    }
    else if (strncmp(payload, HA_HALF, len) == 0){
      hoermannEngine->halfPositionDoor();
    }
    else if (strncmp(payload, HA_VENT, len) == 0){
      hoermannEngine->ventilationPositionDoor();
    }
  }
  else if (strcmp(mqttStrings.setpos_topic, topic) == 0){
    hoermannEngine->setPosition(atoi(lastCommandPayload));
  }

}

void sendOnline()
{
  mqttClient.publish(mqttStrings.availability_topic, 0, true, HA_ONLINE);
}

void setWill()
{
  mqttClient.setWill(mqttStrings.availability_topic, 0, true, HA_OFFLINE);
}

void sendDebug(char *key, String value)
{
  JsonDocument doc;
  char payload[1024];
  doc["reset-reason"] = esp_reset_reason();
  doc["debug"] = hoermannEngine->state->debugMessage;
  serializeJson(doc, payload);
  mqttClient.publish(mqttStrings.debug_topic, 0, false, payload);  //uint16_t publish(const char* topic, uint8_t qos, bool retain, const char* payload = nullptr, size_t length = 0)
}

void sendDiscoveryMessageForBinarySensor(const char name[], const char topic[], const char key[], const char off[], const char on[], const JsonDocument& device)
{

  char full_topic[64];
  sprintf(full_topic, HA_DISCOVERY_BIN_SENSOR, localPrefs->getString(preference_gd_id), key);

  char uid[64];
  sprintf(uid, "%s_binary_sensor_%s", localPrefs->getString(preference_gd_id), key);

  char vtemp[64];
  sprintf(vtemp, "{{ value_json.%s }}", key);

  JsonDocument doc;

  doc["name"] = name;
  doc["state_topic"] = topic;
  doc["availability_topic"] = mqttStrings.availability_topic;
  doc["payload_available"] = HA_ONLINE;
  doc["payload_not_available"] = HA_OFFLINE;
  doc["unique_id"] = uid;
  doc["value_template"] = vtemp;
  doc["payload_on"] = on;
  doc["payload_off"] = off;
  doc["device"] = device;

  char payload[1024];
  serializeJson(doc, payload);
  //-//Serial.write(payload);
  mqttClient.publish(full_topic, 1, true, payload);
}

void sendDiscoveryMessageForAVSensor(const JsonDocument& device)
{
  char full_topic[64];
  sprintf(full_topic, HA_DISCOVERY_AV_SENSOR, localPrefs->getString(preference_gd_id));

  char uid[64];
  sprintf(uid, "%s_sensor_availability", localPrefs->getString(preference_gd_id));
  JsonDocument doc;

  doc["name"] = localPrefs->getString(preference_gd_avail);
  doc["state_topic"] = mqttStrings.availability_topic;
  doc["unique_id"] = uid;
  doc["device"] = device;

  char payload[1024];
  serializeJson(doc, payload);
  //-//Serial.write(payload);
  mqttClient.publish(full_topic, 1, true, payload);
}

void sendDiscoveryMessageForSensor(const char name[], const char topic[], const char key[], const JsonDocument& device, const char device_class[] = "", const char unit[] = "")
{

  char full_topic[64];
  sprintf(full_topic, HA_DISCOVERY_SENSOR, localPrefs->getString(preference_gd_id), key);

  char uid[64];
  sprintf(uid, "%s_sensor_%s", localPrefs->getString(preference_gd_id), key);

  char vtemp[64];
  //small workaround to get the value as float
  if (key == "hum" || key == "temp" || key == "pres"){
    sprintf(vtemp, "{{ value_json.%s | float }}", key);
  } else {
    sprintf(vtemp, "{{ value_json.%s }}", key);
  }

  JsonDocument doc;

  doc["name"] = name;
  doc["state_topic"] = topic;
  doc["availability_topic"] = mqttStrings.availability_topic;
  doc["payload_available"] = HA_ONLINE;
  doc["payload_not_available"] = HA_OFFLINE;
  doc["value_template"] = vtemp;
  doc["device"] = device;
  
  //Only set device class if set
  if(device_class != "") {
    doc["device_class"] = device_class;
  }

  doc["unit_of_measurement"] = unit;
  doc["unique_id"] = uid;
  
  // overwrite device class if special key
  if (key == "hum") {
    doc["state_class"] = "measurement";
    doc["unit_of_measurement"] = "%";
    doc["device_class"] = "humidity";
  } else if (key == "temp") {
    doc["state_class"] = "measurement";
    doc["unit_of_measurement"] = "°C";
    doc["device_class"] = "temperature";
  } else if (key == "pres") {
    doc["state_class"] = "measurement";
    doc["unit_of_measurement"] = "hPa";
    doc["device_class"] = "pressure";
  }

  char payload[1024];
  serializeJson(doc, payload);
  //-//Serial.write(payload);
  mqttClient.publish(full_topic, 1, true, payload);
}

void sendDiscoveryMessageForDebug(const char name[], const char key[], const JsonDocument& device)
{

  char command_topic[64];
  sprintf(command_topic, mqttStrings.st_cmd_topic_var.c_str(), mqttStrings.debug_topic);

  char full_topic[64];
  sprintf(full_topic, HA_DISCOVERY_TEXT, localPrefs->getString(preference_gd_id), key);

  char uid[64];
  sprintf(uid, "%s_text_%s", localPrefs->getString(preference_gd_id), key);

  char vtemp[64];
  sprintf(vtemp, "{{ value_json.%s }}", key);

  JsonDocument doc;

  doc["name"] = name;
  doc["state_topic"] = mqttStrings.debug_topic;
  doc["command_topic"] = command_topic;
  doc["availability_topic"] = mqttStrings.availability_topic;
  doc["payload_available"] = HA_ONLINE;
  doc["payload_not_available"] = HA_OFFLINE;
  doc["unique_id"] = uid;
  doc["value_template"] = vtemp;
  doc["device"] = device;

  char payload[1024];
  serializeJson(doc, payload);
  //-//Serial.write(payload);
  mqttClient.publish(full_topic, 1, true, payload);
}

void sendDiscoveryMessageForSwitch(const char name[], const char discovery[], const char topic[], const char off[], const char on[], const char icon[], const JsonDocument& device, bool optimistic = false)
{
  char command_topic[64];
  sprintf(command_topic, mqttStrings.st_cmd_topic_var.c_str(), topic);

  char full_topic[64];
  sprintf(full_topic, discovery, localPrefs->getString(preference_gd_id), topic);

  char value_template[64];
  sprintf(value_template, "{{ value_json.%s }}", topic);

  char uid[64];
  if (discovery == HA_DISCOVERY_LIGHT){
    sprintf(uid, "%s_light_%s",localPrefs->getString(preference_gd_id), topic);
  }
  else{
    sprintf(uid, "%s_switch_%s",localPrefs->getString(preference_gd_id), topic);
  }

  JsonDocument doc;

  doc["name"] = name;
  doc["state_topic"] = mqttStrings.state_topic;
  doc["command_topic"] = command_topic;
  doc["payload_on"] = on;
  doc["payload_off"] = off;
  doc["icon"] = icon;
  doc["availability_topic"] = mqttStrings.availability_topic;
  doc["payload_available"] = HA_ONLINE;
  doc["payload_not_available"] = HA_OFFLINE;
  doc["unique_id"] = uid;
  doc["value_template"] = value_template;
  doc["optimistic"] = optimistic;
  doc["device"] = device;

  char payload[1024];
  serializeJson(doc, payload);
  //-//Serial.write(payload);
  mqttClient.publish(full_topic, 1, true, payload);
}

void sendDiscoveryMessageForCover(const char name[], const char topic[], const JsonDocument& device)
{

  char command_topic[64];
  sprintf(command_topic, mqttStrings.st_cmd_topic_var.c_str(), topic);

  char full_topic[64];
  sprintf(full_topic, HA_DISCOVERY_COVER, localPrefs->getString(preference_gd_id), topic);

  char uid[64];
  sprintf(uid, "%s_cover_%s", localPrefs->getString(preference_gd_id), topic);

  JsonDocument doc;
 //if it didn't work try without state topic.
  doc["name"] = name;
  doc["state_topic"] = mqttStrings.state_topic;
  doc["command_topic"] = command_topic;
  doc["position_topic"] = mqttStrings.pos_topic;
  doc["set_position_topic"] = mqttStrings.setpos_topic;
  doc["position_open"] = 100;
  doc["position_closed"] = 0;

  doc["payload_open"] = HA_OPEN;
  doc["payload_close"] = HA_CLOSE;
  doc["payload_stop"] = HA_STOP;
  #ifdef AlignToOpenHab
    doc["value_template"] = "{{ value_json.doorposition }}";
  #else
    doc["value_template"] = "{{ value_json.doorstate }}";
  #endif
  doc["state_open"] = HA_OPEN;
  doc["state_opening"] = HA_OPENING;
  doc["state_closed"] = HA_CLOSED;
  doc["state_closing"] = HA_CLOSING;
  doc["state_stopped"] = HA_STOP;
  doc["availability_topic"] = mqttStrings.availability_topic;
  doc["payload_available"] = HA_ONLINE;
  doc["payload_not_available"] = HA_OFFLINE;
  doc["unique_id"] = uid;
  doc["device_class"] = "garage";
  doc["device"] = device;

  char payload[1024];
  serializeJson(doc, payload);
  //-//Serial.write(payload);
  mqttClient.publish(full_topic, 1, true, payload);
}
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
void loop(){
  ElegantOTA.loop();
}

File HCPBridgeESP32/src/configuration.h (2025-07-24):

#ifndef CONFIGURATION_H_
    #define CONFIGURATION_H_
    
    // Please change on every new firmware builds!
    const char *HA_VERSION = "0.1.0.1";

    // WIFI Hostname
    const char HOSTNAME[]   = "HCPBRIDGE";

    // Station -> set AP_ACTIF to false if you wanna use password from config file
    const bool AP_ACTIF = (bool)true;
    const char* STA_SSID   = "";
    const char* STA_PASSWD = "";

    //RS485 pins
    #ifdef CONFIG_IDF_TARGET_ESP32S3
        #ifdef M5STACK
            #define PIN_TXD 13
            #define PIN_RXD 15          
        #else
            #define PIN_TXD 17
            #define PIN_RXD 18
        #endif
    #else
        #define PIN_TXD 17 // UART 2 TXT - G17
        #define PIN_RXD 16 // UART 2 RXD - G16
    #endif

    // MQTT
    #define DEVICE_ID "hcpbridge"
    const char ID_LENGTH = 16;
    const char DEVICENAME[] = "Garage Door";
    const char *MQTTSERVER = "192.168.1.100";
    const int MQTTPORT = 1883;
    const char MQTTUSER[] = "mqtt";
    const char MQTTPASSWORD[] = "password";
    const char GD_AVAIL[]= "Garage Door Available";
    const char GD_LIGHT[] = "Garage Door Light";
    const char GD_VENT[] = "Garage Door Vent";
    const char GD_STATUS[] = "Garage Door Status";
    const char GD_DET_STATUS[] = "Garage Door detailed Status";
    const char GD_POSITIOM[] = "Garage Door Position";
    const char GD_MOTION[] = "Garage Door Motion";
    const char GS_TEMP[] = "Garage Temperature";
    const char GS_HUM[] = "Garage Humidity";
    const char GS_PRES[] = "Garage ambient pressure";
    const char GS_FREE_DIST[] = "Garage Free distance";
    const char GS_PARK_AVAIL[] = "Garage park available";
    const char GD_DEBUG[] = "Garage Door Debug";
    const char GD_DEBUG_RESTART[] = "Garage Restart Reason";

    //OpenHab as SmartHome if uncommented. Comment for homeassistant
    //#define AlignToOpenHab

    //OTA Update
    const char* OTA_USERNAME = "admin";
    const char* OTA_PASSWD = "admin";
    
    // MQTT
    const int READ_DELAY = 2000;           // intervall (ms) to update status on mqtt

    #define SENSE_PERIOD 120  //read interval in Seconds of all defined sensors in seconds

    #define temp_threshold 0.5    //only send mqtt msg when temp,pressure or humidity rises this threshold. set 0 to send every status
    #define hum_threshold 1    //only send mqtt msg when temp,pressure or humidity rises this threshold. set 0 to send every status
    #define pres_threshold 1    //only send mqtt msg when temp,pressure or humidity rises this threshold. set 0 to send every status
    #define prox_treshold 10    //only send mqtt msg when distance change this treshold. Set 0 to send every status

    //DS18X20
    #define oneWireBus 4     //GPIO where the DS18B20 is connected to

    // NOTICE: Breadboards should have 2k2 or 3k3 PullUp resistor between SCL and SDA! If not: interferences
    //BME280
    #ifdef HCP_Giffordv2
        #define I2C_SDA 21
        #define I2C_SCL 33
    #else
        #define I2C_SDA 21
        #define I2C_SCL 22
    #endif

    //HC-SR04
    #ifdef HCP_Giffordv2
        #define SR04_TRIGPIN 5
        #define SR04_ECHOPIN 48
    #else
        #define SR04_TRIGPIN 5
        #define SR04_ECHOPIN 18
    #endif
    #define SR04_MAXDISTANCECM 150
    #define SOUND_SPEED 0.034   //define sound speed in cm/uS

    // DHT22
    #define DHTPIN 27
    #define DHTTYPE DHT22

    //HC-SR501
    #ifdef HCP_Giffordv2
        #define SR501PIN 23
    #else
        #define SR501PIN 34
    #endif

    //digital in- and outputs
    #ifdef HCP_Giffordv2
        #define LED1 13
        #define INPUT1 12
        #define INPUT2 14
        #define OUTPUT1 37
        #define OUTPUT2 35
        #define MQ2_ANALOG 36
        #define MQ2_DIG 15
    #endif

    // MQTT strings
    #define HA_DISCOVERY_BIN_SENSOR "homeassistant/binary_sensor/%s/%s/config"
    #define HA_DISCOVERY_AV_SENSOR "homeassistant/sensor/%s/available/config"
    #define HA_DISCOVERY_SENSOR "homeassistant/sensor/%s/%s/config"
    #define HA_DISCOVERY_SWITCH "homeassistant/switch/%s/%s/config"
    #define HA_DISCOVERY_COVER "homeassistant/cover/%s/%s/config"
    #define HA_DISCOVERY_LIGHT "homeassistant/light/%s/%s/config"
    #define HA_DISCOVERY_TEXT "homeassistant/text/%s/%s/config"

    // DEBUG
    //#define DEBUG
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

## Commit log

2023-01-17 added configuration.h and added a ds18x20 temp sensor
    [configuration.h]
2023-01-17 added ds18x20 temp sensor
2023-01-17 added temp threshold
    [configuration.h]
2023-01-17 added OTA passwd, fixed lib_deps
    [configuration.h]
2023-01-18 added bme280 sensor
    [configuration.h]
2023-01-18 added asyncwifimanager
    [configuration.h]
2023-01-19 changed mqtt topics to defines
    [configuration.h]
2023-01-19 send mqtt msg only on changed state
    [configuration.h]
2023-01-20 added restart button to webui
2023-01-25 fixed bug when reading sensor while polling modbus
    [main.cpp]
2023-01-26 swapped out sensor task to 2nd core
    [configuration.h]
2023-01-26 added restart button
2023-02-02 modbus corrections
    [configuration.h]
2023-02-02 Webpage translation to eng, add "half open" button
2023-02-02 Add position topic (0-100); cleanup; translation; removed unnecessary topics on MQTT; removed ESP8266 references; moved to Serial2 (pin 16&17) for better compatibility.
2023-02-02 Fix MQTT payload string mismatches
    [main.cpp]
2023-02-02 Pin MQTT to different core of Modbus
2023-02-02 Fix status reporting on cover device of HA
    [main.cpp]
2023-02-02 Update configuration file
    [configuration.h]
2023-02-03 added pr and fixed some configurations
    [configuration.h]
2023-02-04 added serial1 debug and fixed initial sensor check
    [main.cpp]
2023-02-04 fixed wrong sensor discovery
    [main.cpp]
2023-02-05 Faster checks of current status
    [configuration.h]
2023-02-05 added 3d case and updated readme
    [body.STL, lid.STL]
2023-02-05 Add set_position feature
    [configuration.h]
2023-02-07 fixed [webui] light switches back to off if manually toggled Gifford47/HCPBridgeMqtt#5
2023-02-08 Fix "stop" when already open/closed and fix "set_position" when near limit values
    [configuration.h]
2023-03-01 added DEBUG makro on esp restart
    [configuration.h]
2023-03-10 send sensor values on normal mqtt task and added a workaround if i2c hung up
    [main.cpp]
2023-03-10 added I2C on off pin (workaround)
    [configuration.h]
2023-04-13 added build option for openhab
    [configuration.h]
2023-04-24 Cleanup PCB Files
    [ESP32-DivKitC Pro PCB Updated.brd]
2023-04-24 Implementing venting Switch with integration in Webui. Refactoring of mqtt discovery message.
    [configuration.h]
2023-04-28 Implement HC_HCS04 proximity sensor to now if the parking space is available. the distance in CM and the information if park space is available is sent to mqtt
    [configuration.h]
2023-04-28 Comment AligToOpenHab
    [configuration.h]
2023-06-09 added debug options
    [configuration.h]
2023-06-09 add debug Mqtt discovery and message. Correct some VtaskDelay locations
    [hoermann.h, main.cpp]
2023-06-10 Replace AsyncWifiManager with Native Wifi see commit dd0236011585e04e38be4e23c033a697d71487e8 Remove Restart Button as it only for Dev pupose 8dd3e7327cfc5230b7a48e665b8321525c305600
    [configuration.h]
2023-06-12 Rewrite AsyncMqttClient setup to handle connection lose without crashing Gifford47/HCPBridgeMqtt#11
    [main.cpp]
2023-06-15 force send mqtt update at connect to mqtt event. Fix sending sensor data when USE_HCSR04 is undefined.
    [main.cpp]
2023-06-20 disable debugging
    [configuration.h]
2023-06-25 Fix Vent Status https://github.com/14yannick/HCPBridgeMqtt/issues/6#issuecomment-1606131998
    [configuration.h]
2023-07-01 updated config
    [configuration.h]
2023-07-01 fix ventting payload
    [configuration.h]
2023-07-01 small fix
    [configuration.h]
2023-07-11 Prepare for pull request
    [configuration.h]
2023-07-11 Prepare for merge
    [configuration.h]
2023-07-11 PCB update folder structure and add missing files
    [ESP32-DivKitC Pro PCB Updated.brd]
2023-07-12 cleaned configuration
    [configuration.h]
2023-07-12 vent correction
    [configuration.h]
2023-07-12 added build environments
    [configuration.h]
2023-07-18 corrected build flags for sensors
    [configuration.h]
2023-07-19 Variable directly defined in hoermann.h
    [configuration.h]
2023-07-20 create Variable for Device name/id
    [configuration.h]
2023-07-21 Implement Variables for device ID
    [configuration.h]
2023-07-21 replace hardcoded garagedoor id
    [main.cpp]
2023-07-22 Define Text variable in config file for MQTT entity names.
    [configuration.h]
2023-07-22 added support for ESP32 S3 based boards
    [configuration.h]
2023-07-23 rearranged some config
    [configuration.h]
2023-08-03 changed content of DEVICE_ID to something different than DEVICENAME to abide by home assistants new MQTT naming rules starting with version 2024.2.0. (Issue #30)
    [configuration.h]
2023-08-03 Fix Issue Loss of WIFI results in WIFI connect loop #31 Reconnect timer was cleared after reconnect Close #31.
    [main.cpp]
2023-08-03 Added Config over webui and AP for initial Setup
    [configuration.h]
2023-08-03 added esp32 target
2023-08-04 Fix Issue Loss of WIFI results in WIFI connect loop #31 Stop Reconnect timer after reconnect
    [main.cpp]
2023-08-13 Redesign preferences Handling
    [configuration.h]
2023-08-14 Implemented the merge request added dht22 sensor #36
    [configuration.h]
2023-08-14 Redesign Preference Handling first test with web gui check
    [main.cpp, preferencesKeys.h]
2023-08-18 redesign preferences add TXD and RXD in build flags for change from default.
    [configuration.h]
2023-08-30 moved hcsr04_maxdistanceCm to configuration.h
    [configuration.h]
2023-08-30 added motion sensor HC-SR501
    [configuration.h]
2023-08-31 Handle config variables in preferences to add the possibility to change them in the web UI
    [configuration.h]
2023-09-01 case sensitive extension
    renaming extension
2023-09-01 Correct Build Flags and add RS485 pins back in config
    [configuration.h]
2023-09-01 adding more preference in webgui
    [configuration.h]
2023-09-04 Add additional element in Preferences
    [configuration.h]
2023-09-04 Fix issue #43 where ESP32 still is in AP mode
    [main.cpp]
2023-09-05 add a reset functionality on boot longpress. #43
    [main.cpp, preferencesKeys.h]
2023-09-07 Reset Preferences when pressing 5 seconds on the boot button. Fix some preferences Handling issues. Still an error on preasure and proximity threshold not displayed in Web Ui
    [main.cpp, preferencesKeys.h]
2023-09-14 Small fix in lenght of json as manufacturer is missing in mqtt message.
    [main.cpp]
2023-09-26 changed wifi AP logic, fixed ui texts
    [configuration.h]
2023-10-22 fixed sr501 sensor in preferences
    [configuration.h]
2023-12-18 add force update sensors after predefined time
2023-12-18 corrected seconds to ms
    [main.cpp]
2024-01-05 Fix issue #48 set_position does not work over MQTT
    [main.cpp]
2024-01-08 Add instructions for Az Delivery's ESP32
    That cheap modules has misleading labelling for beginners.
2024-01-10 add deviceName in webui
2024-01-11 convert sensor values to float
2024-01-12 Version Bump to 0.0.6.1 for release of builds. Small adjustment platformio.ini file to build all firmeware
    [configuration.h]
2024-01-12 Update the dependencies to the actual version. Replace Dynamic and Static Json to Jsondocument
    [hoermann.h, main.cpp]
2024-01-22 Fixes to DHT22 sensor code. Code used DHT_VCC_PIN like with BME280 to bring VCC on before polling, however it was also used as DATA pin with DHT library so whole VCC logic was pointless. As DHT22 doe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
    Additionally enhanced MQTT messages to include state_class, device_class and unit_of_measurement so HA will properly handle sensors without manual YAML.
    [configuration.h]
2024-01-26 Fixed a bug in MQTT messages introduced in PR #56, state_class: measurement was added for all sensor messages, but there were non-measurement sensors as well (status and detailed status) which then c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
    [main.cpp]
2024-01-28 Added "device_class" and "unit_of_measurement" properties to "sendDiscoveryMessageForSensor".
2024-02-02 fixed issue with missing discovery of sensors
    [main.cpp]
2024-02-02 removed vcc toggle for BME
    [configuration.h]
2024-02-02 added temp,hum sensor values to ui
2024-02-04 revert sta settings
    [configuration.h]
2024-02-09 fixed sensor design commit c5d726f
2024-02-14 Fixed a refresh bug on the bme and added infos to ui (#67)
    * fixed wrong bme280 thresholds
    [main.cpp]
2024-02-21 refactoring sensor ui design
2024-06-28 Update configuration.h
    version update
    [configuration.h]
2024-07-03 fixed id length of mqtt client id
    [configuration.h]
2024-07-04 cleanup project
    [ESP32-DivKitC Pro PCB Updated.brd, body.STL, lid.STL]
2024-07-08 fixed a wrong json response for sensor builds
    [main.cpp]
2024-07-08 fixed sensor data shown in ui
    [main.cpp]
2024-09-17 Updated to elegantOTA and fixed libs
    [configuration.h]
2024-11-15 bumped esp sdk, added gifford rev.2, disabled http restart option
    [configuration.h]
2024-11-29 workaround for #88 and added dht hum to webui
    [main.cpp]
2024-11-30 removed i2c onoff pin which suddenly used gpio0
2025-07-24 UART 2
    [configuration.h]
